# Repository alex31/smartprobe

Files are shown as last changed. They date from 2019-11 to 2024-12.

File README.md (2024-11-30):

# SMARTPROBE Pitot3D device

Smartprobe is an autonomous pitot3d tube that is designed to be mounted on a drone.
It records relative wind speed and angles, stores them on sdcard, and stream data on a serial line.

#### *Disclaimer : software was still in alpha stage when the project development was stopped in fall 2021*

## Installation

### The easy way
use the latest binary found under GitHub Releases

### You really want to compile it ?
### Dependencies installation 

>cross compilation and Perl library for the boardGen.pl tool :

``` shell
sudo apt install build-essential gcc-arm-none-eabi gdb-multiarch \
         default-jre libmodern-perl-Perl \
	 libxml-libxml-Perl libfile-which-Perl \
	 dfu-util
	 
sudo cpan -i String/LCSS.pm
```
> to use bmpflash when flashing with a Black Magic Probe or Criquet Probe
``` shell
sudo usermod -a -G dialout $USER
```
### optional : stm32cubemx install from stmicroelectronics website:
https://www.st.com/en/development-tools/stm32cubemx.html
(boardGen.pl script needs xml MCU description files)
If stm32cubemx is not found, a pregenerated board.h is used, you won't be able to modify pin assignation

### clone of GitHub repository and submodules :
``` shell
git clone --recursive https://github.com/alex31/smartprobe.git
cd smartprobe
git submodule update --init --recursive
```

### build firmware in release mode
``` shell
make clean; make BUILD=SIZE
```

### flash firmware in release mode
In dfu mode :
plug micro-USB cable (no need to power supply)
``` shell
make BUILD=SIZE dfuflash

```
In swd mode :
plug swd cable (need to power supply smartprobe)
``` shell
make BUILD=SIZE flash
``` 

## Usage

### µSD Card
It is mandatory to install a micro sd card :
- SD should be formatted with FAT32 or ExFAT filesystem.
- configuration is read from SD
- wind data is stored on the SD
- reading/writing SD can be done
  - offline : SD must be removed
  - online : plug the smartprobe via USB (with SD installed) on a computer, and it will be shown like a USB storage device

### Connector J3 at the back
The Molex connector at the back contains  :  
- power in : Vin should be between 7 and 20 Volts
- bootloader mode switch (connect pin5 with pin6, then power up the smartprobe)
  -bootloader mode is to be used to flash the firmware in the smartprobe
- USB to mount the sdcard as a USB storage device
- UART which can be used for multiple purposes (choice is made in configuration file)

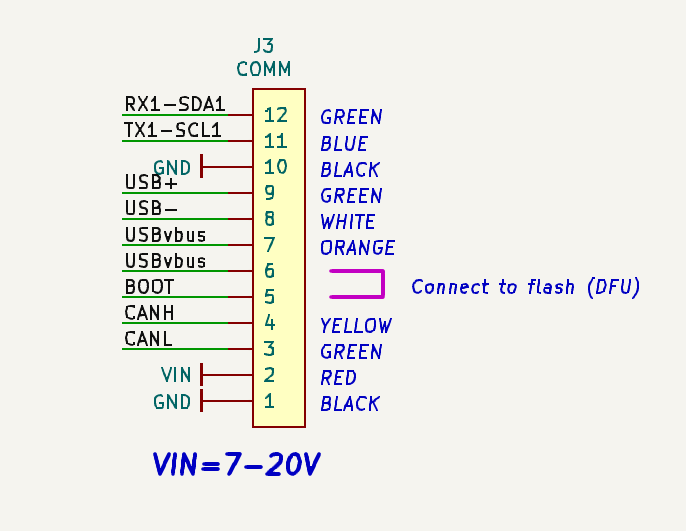
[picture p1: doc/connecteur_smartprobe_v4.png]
Molex connector wiring
  

### Parameters
- firmware parameters are read from the SD at start, in a file named ***smartprobe.conf***
- if a file named smartprobe.conf is not found, it will be created, all the fields set at their default value
- the most accurate and up-to-date definitions (with default and range) for each field can be found in source file  
*source/confParameters.hpp*
- here is a list of parameters (details are missing, confParameters.hpp reading is advised)

|Parameter				| Description 	| default 
|---				| ---  	| ---
|syslog.filename			| name of the file where system events are logged	|syslog
|sensorslog.filename			| name of the file where sensors data are logged	|sensors
|thread.frequency.d_press		| differential pressure sampling frequency  		|100
|thread.frequency.imu			| IMU sampling frequency 				|100
|thread.frequency.stream_console	| frequency of messages on the console			|10
|thread.frequency.transmit_uart		| frequency of messages on serial link			|100
|ahrs.type				| type of AHRS : raw, headless, or complete		|headless_ahrs
|ahrs.output				| ahrs output format : euler or quaternion		|euler
|uart.mode				| no_used or pprz or nmea_in or ubx_in			|pprz
|pprz.message				| pprz msg to stream data : aeroprobe or smartprobe	|aeroprobe
|uart.baud				| Baud rate of the uart in the range 9600..460800	|115200
|canbus.mode				| not yet implemented					|
|canbus.id				| not yet implemented					|
|sensor.barometer.temperatureBias	| temperature bias of the measured exterior air		|-5
|sensor.barometer.lpf			| barometer clock divider (see LPS33HW datasheet)	|div2
|sensor.barometer.odr			| barometer output data rate (see LPS33HW datasheet)	|50hz
|sensor.d_press.fetched			| diff pressure param fetched : press or press + temp	|P+T
|sensor.d_press.fetchTempFrequency	| diff pressure temp frequency fetching			|1<<
|sensor.imu.accrate			| imu acc fetching rate (see ICM20600 datasheet)	|1khz_bw99
|sensor.imu.gyrorange			| gyro range [250 .. 2000] degrees per seconds		|250_dps
|sensor.imu.accrange			| acc range [2 .. 16] G					|2g
|sensor.imu.estimationLoopDuration_ms	| ahrs calibration duration [10 .. 4000] milliseconds	|500
|airspeed.rho				| estimated (0) or fixed in the range [0.1 .. 2]	|0(force estimation)
|airspeed.calibration.m11		| transformation matrix	from the			|1.15
|airspeed.calibration.m12		| calibration process					|0
|airspeed.calibration.m13		| default values can be used to verify that		|0
|airspeed.calibration.m14		| the smartprobe roughly works, but should not be	|6
|airspeed.calibration.m15		| used to make actual measures				|6
|airspeed.calibration.m21		| 							|0
|airspeed.calibration.m22		| 							|15
|airspeed.calibration.m23		| 							|0
|airspeed.calibration.m24		| 							|0
|airspeed.calibration.m25		| 							|0
|airspeed.calibration.m31		| 							|0
|airspeed.calibration.m32		| 							|0
|airspeed.calibration.m33		| 							|11
|airspeed.calibration.m34		| 							|0
|airspeed.calibration.m35		|		 					|0
|airspeed.calibration.bias.velocity	|bias on air velocity (from calibration)		|0
|airspeed.calibration.bias.alpha	|bias on alfa angle (from calibration)			|0
|airspeed.calibration.bias.beta 	|bias on beta angle (from calibration)			|0
|led.mode				|status or airspeed					|status
|					|							|

## Calibration
Smartprobe should be calibrated in a wind tunnel before use. The calibration matrix values should then be written in the configuration file instead of the default values.

### Calibration procedure :
...TO BE WRITTEN...

## Development tool
there is a SWD connector on the PCB for connecting a debug probe (Black Magic Probe or STlink V2/V3) which permits debugging with gdb and access to a shell console where errors messages are shown.

## troubleshooting
The led color reflect status of operation (see details below). When error occurs, the error details are logged in the syslog file, on the sdcard, and on debug console if a probe is attached to the internal swd+serial connector.

#### error codes :
- blink green : OK
- blink green and orange : sd card file system is dirty, operation will try to continue, but ultimately, there is a need for filesystem check or reformating
- blink orange : sd card mount has failed
- blink green and white : configuration file error
- blink red : hardware fault detected

..
## Ideas for future developments 
- If external componant (autopilot) stream gps positions and heading, wind in a terrestrial reference frame could be calculated on board
- add USB CDC endoint to the existing USB storage endpoint to output serial console shell via USB
- stream UAVCAN messages on the CAN 2.0B interface

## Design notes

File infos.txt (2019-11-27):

             _______           _____                   
            |__   __|         |  __ \                  
               | |      ___   | |  | |    ___          
               | |     / _ \  | |  | |   / _ \         
               | |    | (_) | | |__| |  | (_) |        
               |_|     \___/  |_____/    \___/         

   ° fix
        * tester fix frozen
	* workerClass.hpp :
	  ø faire l'init en thread context (necessaire pour les event listener, mutex, ...)
	  ø run : remplacer while (true) {...}  par do {...} while (time != TIME_INFINITE)
	* remplacer les DebugTrace par des logError(severity, "string")
	* log de la revision de firmware sha git + date/time de compilation
	* remplacer le log de compteur par des données capteur
	* recoder la partie  FCNTL_WRITE de sdLog.c pour factoriser le code

   ° écrire des modules

	* lecture fichier de conf
	* version qui envoie les données brutes sur la liaison série et la sdcard pour Murat
	* ahrs 2 angles (sans compas)
	* eigen ?
	* watchdog IWDG -> test au boot, si il y a eu hardfault -> log
	* recup de données gps -> ref horaire, calcul du cap, choix du format dans le fichier de conf :
	  ø nmea ou trame pprz (ou autre ?)
	* embarquer micro python pour coder du comportement via le fichier de conf sans avoir à reflasher ?

             _____     __  __    ___          
            |  __ \   |  \/  |  / _ \         
            | |  | |  | \  / | | |_| |        
            | |  | |  | |\/| | |  _  |        
            | |__| |  | |  | | | | | |        
            |_____/   |_|  |_| |_| |_|        
                    _                                                     
                   | |                                                    
             ___   | |_    _ __    ___    __ _   _ __ ___    ___          
            / __|  | __|  | '__|  / _ \  / _` | | '_ ` _ \  / __|         
            \__ \  \ |_   | |    |  __/ | (_| | | | | | | | \__ \         
            |___/   \__|  |_|     \___|  \__,_| |_| |_| |_| |___/         

#define STM32_ADC_ADC1_DMA_STREAM           STM32_DMA_STREAM_ID(2, 4)
#define STM32_SDC_SDMMC1_DMA_STREAM         STM32_DMA_STREAM_ID(2, 6)
#define STM32_SPI_SPI1_RX_DMA_STREAM        STM32_DMA_STREAM_ID(2, 0)
#define STM32_SPI_SPI1_TX_DMA_STREAM        STM32_DMA_STREAM_ID(2, 3)
#define STM32_I2C_I2C2_RX_DMA_STREAM        STM32_DMA_STREAM_ID(1, 3)
#define STM32_I2C_I2C2_TX_DMA_STREAM        STM32_DMA_STREAM_ID(1, 7)
#define STM32_I2C_I2C4_RX_DMA_STREAM        STM32_DMA_STREAM_ID(1, 2)
#define STM32_I2C_I2C4_TX_DMA_STREAM        STM32_DMA_STREAM_ID(1, 5)

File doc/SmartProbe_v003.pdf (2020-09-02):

## SmartProbe_v003 Project Configuration Report

# 1. Description

## 1.1. Project

Project Name | SmartProbe_v003
Board Name | custom
Generated with: | STM32CubeMX 5.6.0
Date | 03/17/2020

## 1.2. MCU

MCU Series | STM32F7
MCU Line | STM32F7x7
MCU name | STM32F777VIHx
MCU Package | TFBGA100
MCU Pin number | 100

# 2. Pinout Configuration

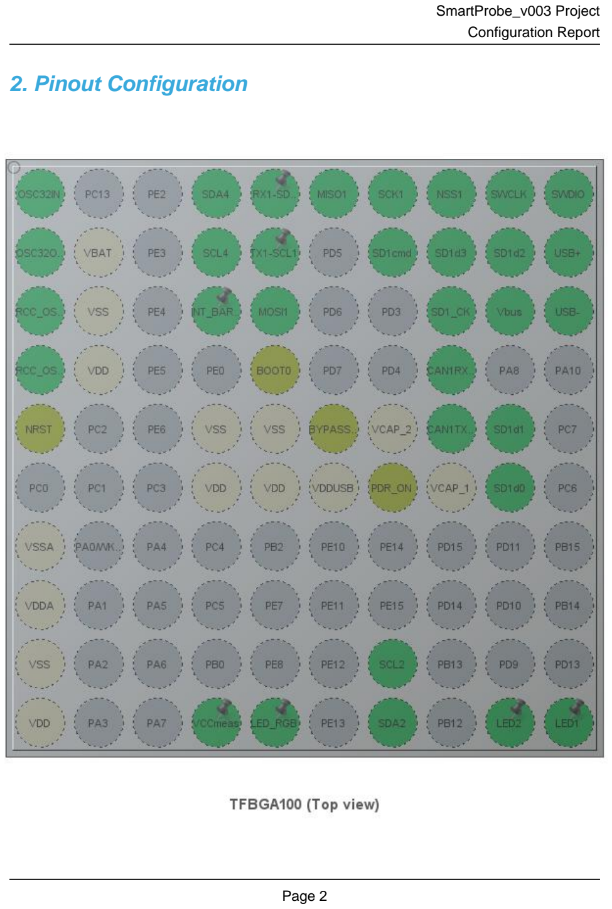
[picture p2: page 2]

# 3. Pins Configuration

Pin Number TFBGA100 | Pin Name (function after reset) | Pin Type | Alternate Function(s) | Label
A1 | PC14/OSC32_IN | I/O | RCC_OSC32_IN | OSC32IN
A4 | PB9 | I/O | I2C4_SDA | SDA4
A5 | PB7 | I/O | USART1_RX | RX1-SDA1
A6 | PB4 | I/O | SPI1_MISO | MISO1
A7 | PB3 | I/O | SPI1_SCK | SCK1
A8 | PA15 | I/O | SPI1_NSS | NSS1
A9 | PA14 | I/O | SYS_JTCK-SWCLK | SWCLK
A10 | PA13 | I/O | SYS_JTMS-SWDIO | SWDIO
B1 | PC15/OSC32_OUT | I/O | RCC_OSC32_OUT | OSC32OUT
B2 | VBAT | Power
B4 | PB8 | I/O | I2C4_SCL | SCL4
B5 | PB6 | I/O | USART1_TX | TX1-SCL1
B7 | PD2 | I/O | SDMMC1_CMD | SD1cmd
B8 | PC11 | I/O | SDMMC1_D3 | SD1d3
B9 | PC10 | I/O | SDMMC1_D2 | SD1d2
B10 | PA12 | I/O | USB_OTG_FS_DP | USB+
C1 | PH0/OSC_IN | I/O | RCC_OSC_IN
C2 | VSS | Power
C4 | PE1 * | I/O | GPIO_Input | INT_BARO
C5 | PB5 | I/O | SPI1_MOSI | MOSI1
C8 | PC12 | I/O | SDMMC1_CK | SD1_CK
C9 | PA9 | I/O | USB_OTG_FS_VBUS | Vbus
C10 | PA11 | I/O | USB_OTG_FS_DM | USB-
D1 | PH1/OSC_OUT | I/O | RCC_OSC_OUT
D2 | VDD | Power
D5 | BOOT0 | Boot
D8 | PD0 | I/O | CAN1_RX | CAN1RX-RX4
E1 | NRST | Reset
E4 | VSS | Power
E5 | VSS | Power
E6 | BYPASS_REG | Reset
E7 | VCAP_2 | Power
E8 | PD1 | I/O | CAN1_TX | CAN1TX-TX4
E9 | PC9 | I/O | SDMMC1_D1 | SD1d1
F4 | VDD | Power
F5 | VDD | Power

Pin Number TFBGA100 | Pin Name (function after reset) | Pin Type | Alternate Function(s) | Label
F6 | VDDUSB | Power
F7 | PDR_ON | Reset
F8 | VCAP_1 | Power
F9 | PC8 | I/O | SDMMC1_D0 | SD1d0
G1 | VSSA | Power
H1 | VDDA | Power
J1 | VSS | Power
J7 | PB10 | I/O | I2C2_SCL | SCL2
K1 | VDD | Power
K4 | PB1 | I/O | ADC1_IN9 | VCCmeas
K5 | PE9 | I/O | TIM1_CH1 | LED_RGB
K7 | PB11 | I/O | I2C2_SDA | SDA2
K9 | PD8 * | I/O | GPIO_Output | LED2
K10 | PD12 * | I/O | GPIO_Output | LED1

## * The pin is affected with an I/O function

# 4. Clock Tree Configuration

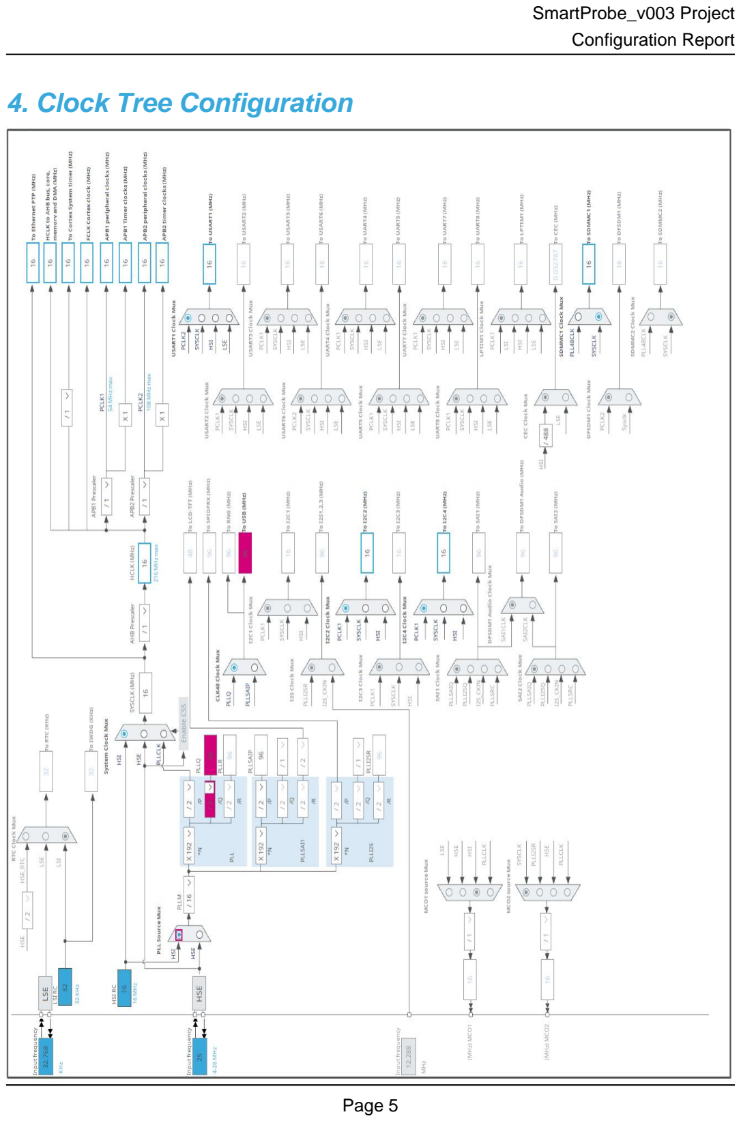
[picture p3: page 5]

# 5. Software Project

## 5.1. Project Settings

Name | Value
Project Name | SmartProbe_v003
Project Folder | /home/alex/DEV/STM32/CHIBIOS/C19DEV/SMARTPROBE_M777/smart_probe
Toolchain / IDE | EWARM V8.32
Firmware Package Name and Version | STM32Cube FW_F7 V1.15.0

## 5.2. Code Generation Settings

Name | Value
STM32Cube MCU packages and embedded software | Copy all used libraries into the project folder
Generate peripheral initialization as a pair of '.c/.h' files | No
Backup previously generated files when re-generating | No
Delete previously generated files when not re-generated | Yes
Set all free pins as analog (to optimize the power consumption) | No

# 6. Power Consumption Calculator report

### 6.1. Microcontroller Selection

Series | STM32F7
Line | STM32F7x7
MCU | STM32F777VIHx
Datasheet | 028294_Rev4

### 6.2. Parameter Selection

Temperature | 25
Vdd | 3.3

### 6.3. Battery Selection

Battery | Alkaline(9V)
Capacity | 625.0 mAh
Self Discharge | 0.3 %/month
Nominal Voltage | 9.0 V
Max Cont Current | 200.0 mA
Max Pulse Current | 0.0 mA
Cells in series | 1
Cells in parallel | 1

## 6.4. Sequence

Step | Step1 | Step2
Mode | RUN | STOP_UDM (Under Drive)
Vdd | 3.3 | 3.3
Voltage Source | Battery | Battery
Range | Scale1-High | No Scale
Fetch Type | ICTM FLASH-SingleBank REGON | n/a
CPU Frequency | 216 MHz | 0 Hz
Clock Configuration | HSE PLL | Regulator_LP Flash-PwrDwn
Clock Source Frequency | 4 MHz | 0 Hz

### Peripherals

Additional Cons. | 0 mA | 0 mA
Average Current | 118 mA | 130 µA
Duration | 0.1 ms | 0.9 ms
DMIPS | 462.0 | 0.0
Ta Max | 88.26 | 104.98
Category | In DS Table | In DS Table

## 6.5. RESULTS

Sequence Time | 1 ms | Average Current | 11.92 mA
Battery Life | 2 days, 4 hours | Average DMIPS | 462.24 DMIPS

## 6.6. Chart

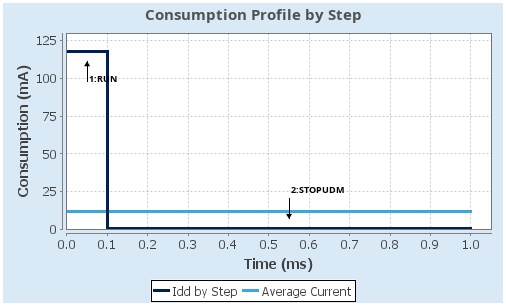
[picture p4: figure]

# 7. IPs and Middleware Configuration

# 7.1. ADC1

## mode: IN9 7.1.1. Parameter Settings:

### ADCs_Common_Settings:

Mode | Independent mode

### ADC_Settings:

Clock Prescaler | PCLK2 divided by 2
Resolution | 12 bits (15 ADC Clock cycles)
Data Alignment | Right alignment
Scan Conversion Mode | Disabled
Continuous Conversion Mode | Disabled
Discontinuous Conversion Mode | Disabled
DMA Continuous Requests | Disabled
End Of Conversion Selection | EOC flag at the end of single channel conversion

### ADC_Regular_ConversionMode:

Number Of Conversion | 1
External Trigger Conversion Source | Regular Conversion launched by software
External Trigger Conversion Edge | None
Rank | 1
Channel | Channel 9
Sampling Time | 3 Cycles

### ADC_Injected_ConversionMode:

Number Of Conversions | 0

### WatchDog:

Enable Analog WatchDog Mode | false

# 7.2. CAN1

## mode: Mode 7.2.1. Parameter Settings:

### Bit Timings Parameters:

Prescaler (for Time Quantum) | 16
Time Quantum | 1000.0 *
Time Quanta in Bit Segment 1 | 1 Time
Time Quanta in Bit Segment 2 | 1 Time

ReSynchronization Jump Width | 1 Time

### Basic Parameters:

Time Triggered Communication Mode | Disable
Automatic Bus-Off Management | Disable
Automatic Wake-Up Mode | Disable
Automatic Retransmission | Disable
Receive Fifo Locked Mode | Disable
Transmit Fifo Priority | Disable

### Advanced Parameters:

Operating Mode | Normal

# 7.3. GPIO

# 7.4. I2C2

## I2C: I2C 7.4.1. Parameter Settings:

### Timing configuration:

I2C Speed Mode | Standard Mode
I2C Speed Frequency (KHz) | 100
Rise Time (ns) | 0
Fall Time (ns) | 0
Coefficient of Digital Filter | 0
Analog Filter | Enabled
Timing | 0x00303D5B

### Slave Features:

Clock No Stretch Mode | Disabled
General Call Address Detection | Disabled
Primary Address Length selection | 7-bit
Dual Address Acknowledged | Disabled
Primary slave address | 0

# 7.5. I2C4

## I2C: I2C 7.5.1. Parameter Settings:

### Timing configuration:

I2C Speed Mode | Standard Mode
I2C Speed Frequency (KHz) | 100
Rise Time (ns) | 0
Fall Time (ns) | 0
Coefficient of Digital Filter | 0
Analog Filter | Enabled
Timing | 0x00303D5B

### Slave Features:

Clock No Stretch Mode | Disabled
General Call Address Detection | Disabled
Primary Address Length selection | 7-bit
Dual Address Acknowledged | Disabled
Primary slave address | 0

# 7.6. RCC

## High Speed Clock (HSE): Crystal/Ceramic Resonator Low Speed Clock (LSE) : Crystal/Ceramic Resonator 7.6.1. Parameter Settings:

### System Parameters:

VDD voltage (V) | 3.3
Flash Latency(WS) | 0 WS (1 CPU cycle)

### RCC Parameters:

HSI Calibration Value | 16
TIM Prescaler Selection | Disabled
HSE Startup Timout Value (ms) | 100
LSE Startup Timout Value (ms) | 5000

### Power Parameters:

Power Over Drive | Disabled
Power Regulator Voltage Scale | Power Regulator Voltage Scale 3

# 7.7. SDMMC1

## Mode: SD 4 bits Wide bus 7.7.1. Parameter Settings:

### SDMMC parameters:

Clock transition on which the bit capture is made Rising transition

SDMMC Clock divider bypass | Disable
SDMMC Clock output enable when the bus is idle | Disable the power save for the clock
SDMMC hardware flow control | The hardware control flow is disabled
SDMMCCLK clock divide factor | 0

# 7.8. SPI1

## Mode: Full-Duplex Master Hardware NSS Signal: Hardware NSS Output Signal 7.8.1. Parameter Settings:

### Basic Parameters:

Frame Format | Motorola
Data Size | 4 Bits
First Bit | MSB First

### Clock Parameters:

Prescaler (for Baud Rate) | 2
Baud Rate | 8.0 MBits/s *
Clock Polarity (CPOL) | Low
Clock Phase (CPHA) | 1 Edge

### Advanced Parameters:

CRC Calculation | Disabled
NSSP Mode | Enabled
NSS Signal Type | Output Hardware

# 7.9. SYS

## Debug: Serial Wire Timebase Source: SysTick

# 7.10. TIM1

## Channel1: PWM Generation CH1 7.10.1. Parameter Settings:

### Counter Settings:

Prescaler (PSC - 16 bits value) | 0
Counter Mode | Up
Counter Period (AutoReload Register - 16 bits value ) | 0

Internal Clock Division (CKD) | No Division
Repetition Counter (RCR - 16 bits value) | 0
auto-reload preload | Disable

### Trigger Output (TRGO) Parameters:

Master/Slave Mode (MSM bit) | Disable (Trigger input effect not delayed)
Trigger Event Selection TRGO | Reset (UG bit from TIMx_EGR)
Trigger Event Selection TRGO2 | Reset (UG bit from TIMx_EGR)

### Break And Dead Time management - BRK Configuration:

BRK State | Disable
BRK Polarity | High
BRK Filter (4 bits value) | 0
BRK Sources Configuration
- Digital Input | Disable
- DFSDM | Disable

### Break And Dead Time management - BRK2 Configuration:

BRK2 State | Disable
BRK2 Polarity | High
BRK2 Filter (4 bits value) | 0
BRK2 Sources Configuration
- Digital Input | Disable
- DFSDM | Disable

### Break And Dead Time management - Output Configuration:

Automatic Output State | Disable
Off State Selection for Run Mode (OSSR) | Disable
Off State Selection for Idle Mode (OSSI) | Disable
Lock Configuration | Off

### PWM Generation Channel 1:

Mode | PWM mode 1
Pulse (16 bits value) | 0
Output compare preload | Enable
Fast Mode | Disable
CH Polarity | High
CH Idle State | Reset

# 7.11. USART1

## Mode: Asynchronous 7.11.1. Parameter Settings:

### Basic Parameters:

Baud Rate | 115200
Word Length | 8 Bits (including Parity)
Parity | None
Stop Bits | 1

### Advanced Parameters:

Data Direction | Receive and Transmit
Over Sampling | 16 Samples
Single Sample | Disable

### Advanced Features:

Auto Baudrate | Disable
TX Pin Active Level Inversion | Disable
RX Pin Active Level Inversion | Disable
Data Inversion | Disable
TX and RX Pins Swapping | Disable
Overrun | Enable
DMA on RX Error | Enable
MSB First | Disable

# 7.12. USB_OTG_FS

## Mode: Device_Only mode: Activate_VBUS 7.12.1. Parameter Settings:

Speed | Device Full Speed 12MBit/s
Low power | Disabled
Link Power Management | Disabled
VBUS sensing | Enabled
Signal start of frame | Disabled

### * User modified value

# 8. System Configuration

# 8.1. GPIO configuration

IP | Pin | Signal | GPIO mode | GPIO pull/up pull down | Max Speed | User Label
ADC1 | PB1 | ADC1_IN9 | Analog mode | No pull-up and no pull-down | n/a | VCCmeas
CAN1 | PD0 | CAN1_RX | Alternate Function Push Pull | No pull-up and no pull-down | Very High * | CAN1RX-RX4
| PD1 | CAN1_TX | Alternate Function Push Pull | No pull-up and no pull-down | Very High * | CAN1TX-TX4
I2C2 | PB10 | I2C2_SCL | Alternate Function Open Drain | Pull-up | Very High * | SCL2
| PB11 | I2C2_SDA | Alternate Function Open Drain | Pull-up | Very High * | SDA2
I2C4 | PB9 | I2C4_SDA | Alternate Function Open Drain | Pull-up | Very High * | SDA4
| PB8 | I2C4_SCL | Alternate Function Open Drain | Pull-up | Very High * | SCL4
RCC | PC14/OSC3 2_IN | RCC_OSC32_IN | n/a | n/a | n/a | OSC32IN
| PC15/OSC3 2_OUT | RCC_OSC32_O UT | n/a | n/a | n/a | OSC32OUT
| PH0/OSC_I N | RCC_OSC_IN | n/a | n/a | n/a
| PH1/OSC_O UT | RCC_OSC_OUT | n/a | n/a | n/a
SDMMC1 | PD2 | SDMMC1_CMD | Alternate Function Push Pull | No pull-up and no pull-down | Very High | SD1cmd
| PC11 | SDMMC1_D3 | Alternate Function Push Pull | No pull-up and no pull-down | Very High | SD1d3
| PC10 | SDMMC1_D2 | Alternate Function Push Pull | No pull-up and no pull-down | Very High | SD1d2
| PC12 | SDMMC1_CK | Alternate Function Push Pull | No pull-up and no pull-down | Very High | SD1_CK
| PC9 | SDMMC1_D1 | Alternate Function Push Pull | No pull-up and no pull-down | Very High | SD1d1
| PC8 | SDMMC1_D0 | Alternate Function Push Pull | No pull-up and no pull-down | Very High | SD1d0
SPI1 | PB4 | SPI1_MISO | Alternate Function Push Pull | No pull-up and no pull-down | Very High * | MISO1
| PB3 | SPI1_SCK | Alternate Function Push Pull | No pull-up and no pull-down | Very High * | SCK1
| PA15 | SPI1_NSS | Alternate Function Push Pull | No pull-up and no pull-down | Very High * | NSS1
| PB5 | SPI1_MOSI | Alternate Function Push Pull | No pull-up and no pull-down | Very High * | MOSI1

IP | Pin | Signal | GPIO mode | GPIO pull/up pull down | Max Speed | User Label
SYS | PA14 | SYS_JTCK-SWCLK | n/a | n/a | n/a | SWCLK
| PA13 | SYS_JTMS-SWDIO | n/a | n/a | n/a | SWDIO
TIM1 | PE9 | TIM1_CH1 | Alternate Function Push Pull | No pull-up and no pull-down | Low | LED_RGB
USART1 | PB7 | USART1_RX | Alternate Function Push Pull | No pull-up and no pull-down | Very High * | RX1-SDA1
| PB6 | USART1_TX | Alternate Function Push Pull | No pull-up and no pull-down | Very High * | TX1-SCL1
USB_OTG_ FS | PA12 | USB_OTG_FS_ DP | Alternate Function Push Pull | No pull-up and no pull-down | Very High * | USB+
| PA9 | USB_OTG_FS_ VBUS | Input mode | No pull-up and no pull-down | n/a | Vbus
| PA11 | USB_OTG_FS_ DM | Alternate Function Push Pull | No pull-up and no pull-down | Very High * | USB-
GPIO | PE1 | GPIO_Input | Input mode | No pull-up and no pull-down | n/a | INT_BARO
| PD8 | GPIO_Output | Output Push Pull | No pull-up and no pull-down | Low | LED2
| PD12 | GPIO_Output | Output Push Pull | No pull-up and no pull-down | Low | LED1

# 8.2. DMA configuration

DMA request | Stream | Direction | Priority
TIM1_CH1 | DMA2_Stream1 | Memory To Peripheral | Low

## TIM1_CH1: DMA2_Stream1 DMA request Settings:

Mode: | Normal
Use fifo: | Disable
Peripheral Increment: | Disable
Memory Increment: | Enable *
Peripheral Data Width: | Half Word
Memory Data Width: | Half Word

# 8.3. NVIC configuration

Interrupt Table | Enable | Preenmption Priority | SubPriority
Non maskable interrupt | true | 0 | 0
Hard fault interrupt | true | 0 | 0
Memory management fault | true | 0 | 0
Pre-fetch fault, memory access fault | true | 0 | 0
Undefined instruction or illegal state | true | 0 | 0
System service call via SWI instruction | true | 0 | 0
Debug monitor | true | 0 | 0
Pendable request for system service | true | 0 | 0
System tick timer | true | 0 | 0
DMA2 stream1 global interrupt | true | 0 | 0
PVD interrupt through EXTI line 16 | unused
Flash global interrupt | unused
RCC global interrupt | unused
ADC1, ADC2 and ADC3 global interrupts | unused
CAN1 TX interrupts | unused
CAN1 RX0 interrupts | unused
CAN1 RX1 interrupt | unused
CAN1 SCE interrupt | unused
TIM1 break interrupt and TIM9 global interrupt | unused
TIM1 update interrupt and TIM10 global interrupt | unused
TIM1 trigger and commutation interrupts and TIM11 global interrupt | unused
TIM1 capture compare interrupt | unused
I2C2 event interrupt | unused
I2C2 error interrupt | unused
SPI1 global interrupt | unused
USART1 global interrupt | unused
SDMMC1 global interrupt | unused
USB On The Go FS global interrupt | unused
FPU global interrupt | unused
I2C4 event interrupt | unused
I2C4 error interrupt | unused

### * User modified value

# 9. Predefined Views - Category view : Current

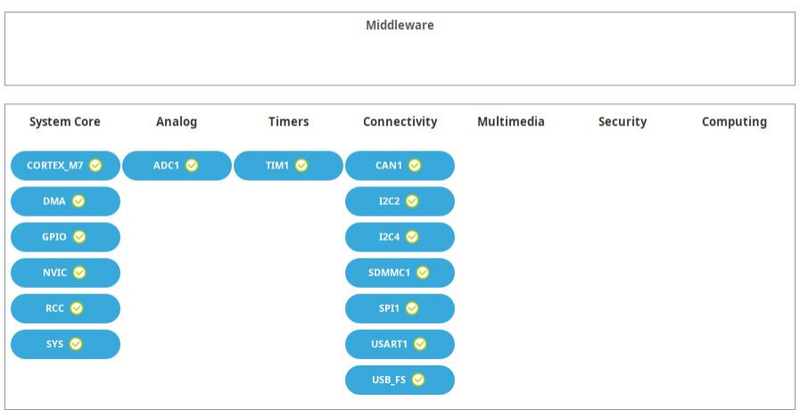
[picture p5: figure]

# 10. Software Pack Report

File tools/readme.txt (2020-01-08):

utilisation de l'interface graphique associée à la smartprobe :

* flasher une smartprobe avec la dernière version du firmware de la branche
  with_ahrs_and_eigen"

* brancher une blackmagic probe pour avoir un convertisseur usb serie

* par defaut, les messages de sortie sont émis, donc rien à faire de ce côté là.

* lancer le script spGui.pl

* ordre des bargraphs : pression absolue, diff1, diff2, diff3

* tout à droite il y a un scale qui permet de regler le gain au niveau de
  l'affichage de la pression differentielle.

* en // les données sont logguées sur la carte SD en fonction des paramètres lu sur le
  fichier smartprobe.conf à la racine de la carte SD

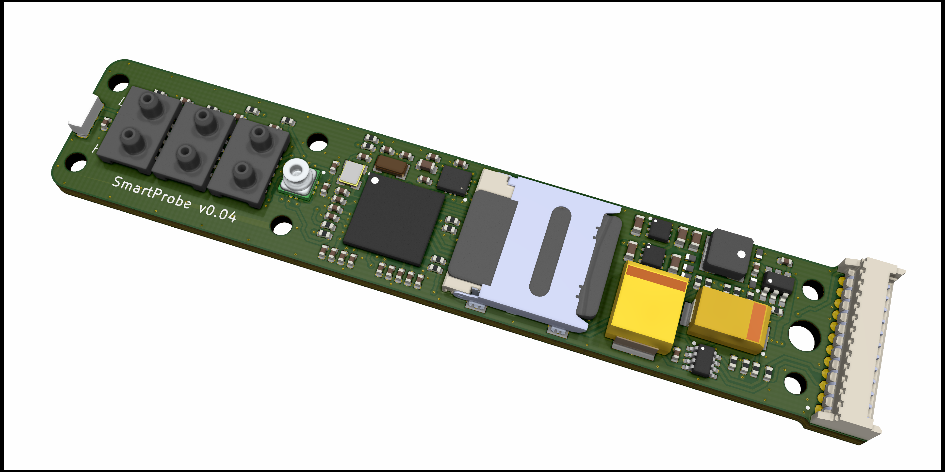
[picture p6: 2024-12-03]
hardware/Pictures/SmartProbe_v004_pcb_top_view.png

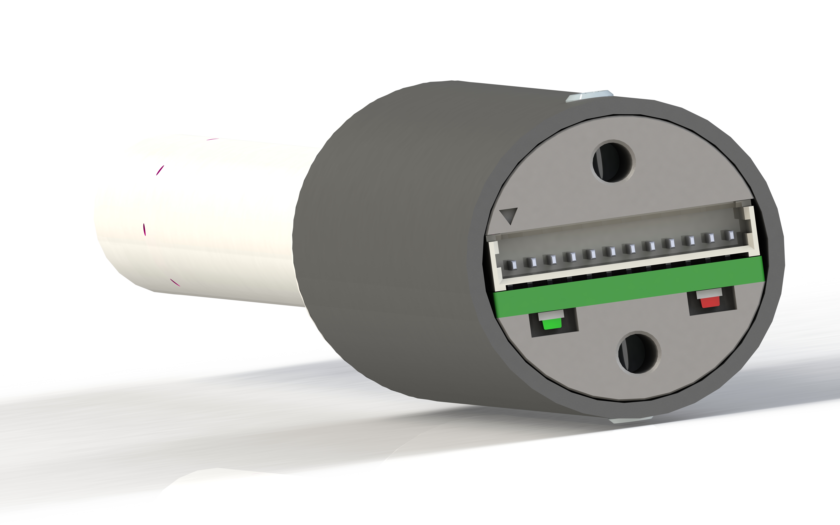
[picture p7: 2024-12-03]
hardware/Pictures/SmartProbe_v004_view7.JPG

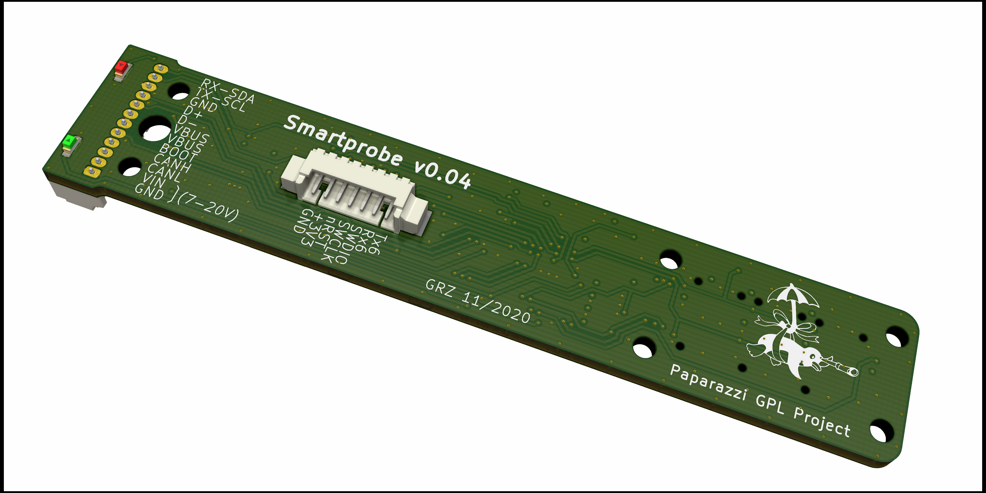
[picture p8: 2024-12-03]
hardware/Pictures/SmartProbe_v004_pcb_bottom_view.png

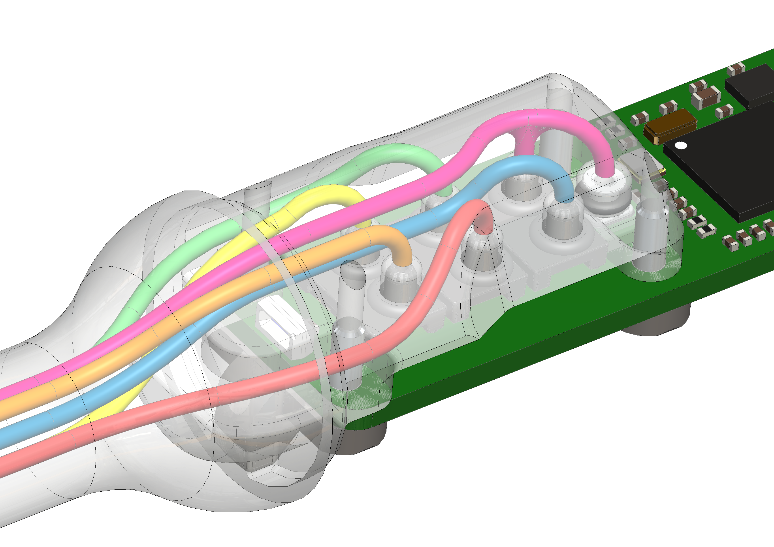
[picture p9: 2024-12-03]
hardware/Pictures/SmartProbe_v004_view4.PNG

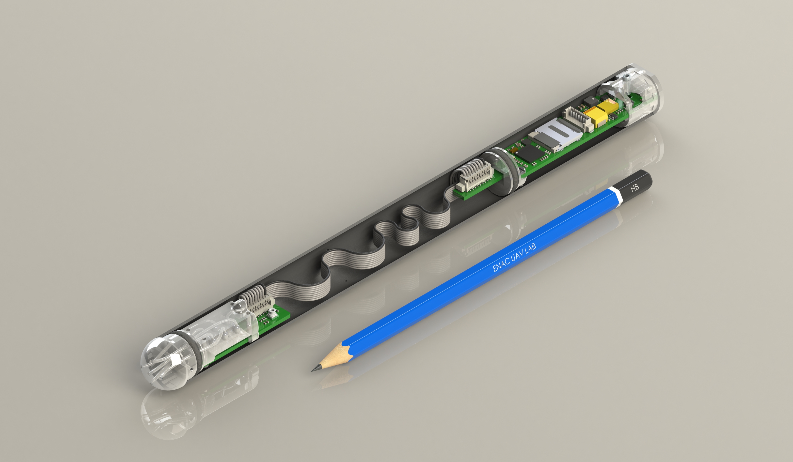
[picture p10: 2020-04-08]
doc/SmartProbe_v003_pencil_1.JPG

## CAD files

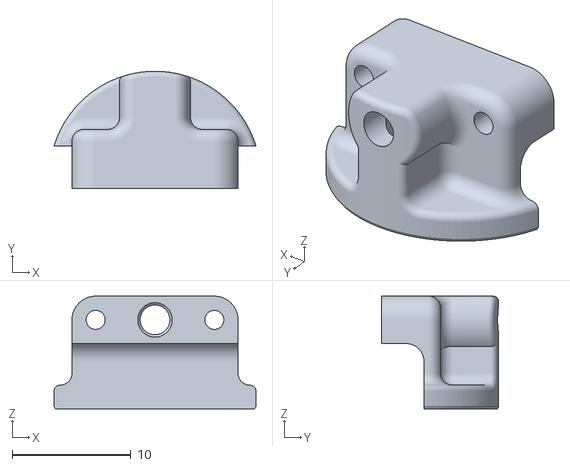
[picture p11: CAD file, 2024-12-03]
hardware/Mechanics/SmartProbe_v004_cap.STL
17.0 x 9.90 x 9.50

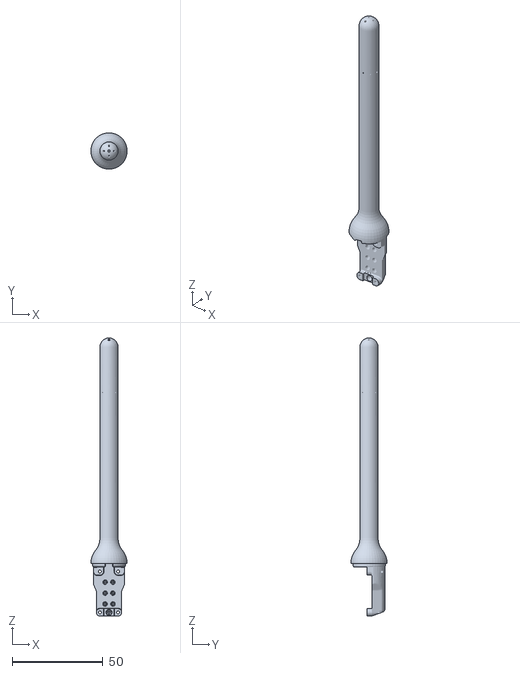
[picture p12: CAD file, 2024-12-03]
hardware/Mechanics/SmartProbe_v004_noze.STL
20.0 x 19.9 x 153.0

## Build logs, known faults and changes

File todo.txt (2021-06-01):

             _______           _____                   
            |__   __|         |  __ \                  
               | |      ___   | |  | |    ___          
               | |     / _ \  | |  | |   / _ \         
               | |    | (_) | | |__| |  | (_) |        
               |_|     \___/  |_____/    \___/         

A CODER:

        * en fonction du choix du format de sortie de l'ahrs :
	  + sortir dans le bon format pour sd (mais pas terminal qui reste en euler)
	  + sortir en pascal au lieu de hPa partout (sd et serial) mais pas terminal qui reste en hPa
	  + sortir en radian partout mais pas terminal qui reste en degrés

	* implementer une directive include dans confFile
	  * mettre les données de calibration dans cet include en rajoutant
	    un parametre "nom de calibration"

	* utilisation du buscan pour chainer les smartprobes

	* ahrs complet qui donne 3 angles si la donnée cap est disponible 

	* calcul d'un vecteur vent dans le repaire terrestre si l'ahrs est
	  en mode 3 angles et que
	   1/ l'autopilote fournit un vecteur vitesse en 3D
	   ou
	   2/ un gps est connecté et permet de calculer le vecteur vitesse en 3D

A AMELIORER :

	* rationaliser utilisation d'allocateur dynamique  :
	  celui de newlib ou tlsf, eliminuer celui de chibios
	* (LOW PRIO) utiliser module UART (DMA) au lieu de serial pour
	             les I/O sur la liaison série ?

	* amélioration des perfos :
    	  + utiliser c++ fmt au lieu de cstdio dans le cas du log texte

        * watchdog IWDG -> test au boot, si il y a eu hardfault -> log

GRANDES LIGNES : 

   ° integration de librairies externes
	* coder du comportement via le fichier de conf sans avoir à reflasher :
	  +  micro python ?
	     OU
	  + langage adhoc en utilisant un parser et un lexer ?

             _____     __  __    ___          
            |  __ \   |  \/  |  / _ \         
            | |  | |  | \  / | | |_| |        
            | |  | |  | |\/| | |  _  |        
            | |__| |  | |  | | | | | |        
            |_____/   |_|  |_| |_| |_|        
                    _                                                     
                   | |                                                    
             ___   | |_    _ __    ___    __ _   _ __ ___    ___          
            / __|  | __|  | '__|  / _ \  / _` | | '_ ` _ \  / __|         
            \__ \  \ |_   | |    |  __/ | (_| | | | | | | | \__ \         
            |___/   \__|  |_|     \___|  \__,_| |_| |_| |_| |___/         

#define STM32_ADC_ADC1_DMA_STREAM           STM32_DMA_STREAM_ID(2, 4)
#define STM32_TIM1_UP_DMA_STREAM	    STM32_DMA_STREAM_ID(2, 5)
#define STM32_TIM1_UP_DMA_CHANNEL	    6
#define STM32_SDC_SDMMC1_DMA_STREAM         STM32_DMA_STREAM_ID(2, 6)
#define STM32_SPI_SPI1_RX_DMA_STREAM        STM32_DMA_STREAM_ID(2, 0)
#define STM32_SPI_SPI1_TX_DMA_STREAM        STM32_DMA_STREAM_ID(2, 3)
#define STM32_I2C_I2C2_RX_DMA_STREAM        STM32_DMA_STREAM_ID(1, 3)
#define STM32_I2C_I2C2_TX_DMA_STREAM        STM32_DMA_STREAM_ID(1, 7)
#define STM32_I2C_I2C4_RX_DMA_STREAM        STM32_DMA_STREAM_ID(1, 2)
#define STM32_I2C_I2C4_TX_DMA_STREAM        STM32_DMA_STREAM_ID(1, 5)

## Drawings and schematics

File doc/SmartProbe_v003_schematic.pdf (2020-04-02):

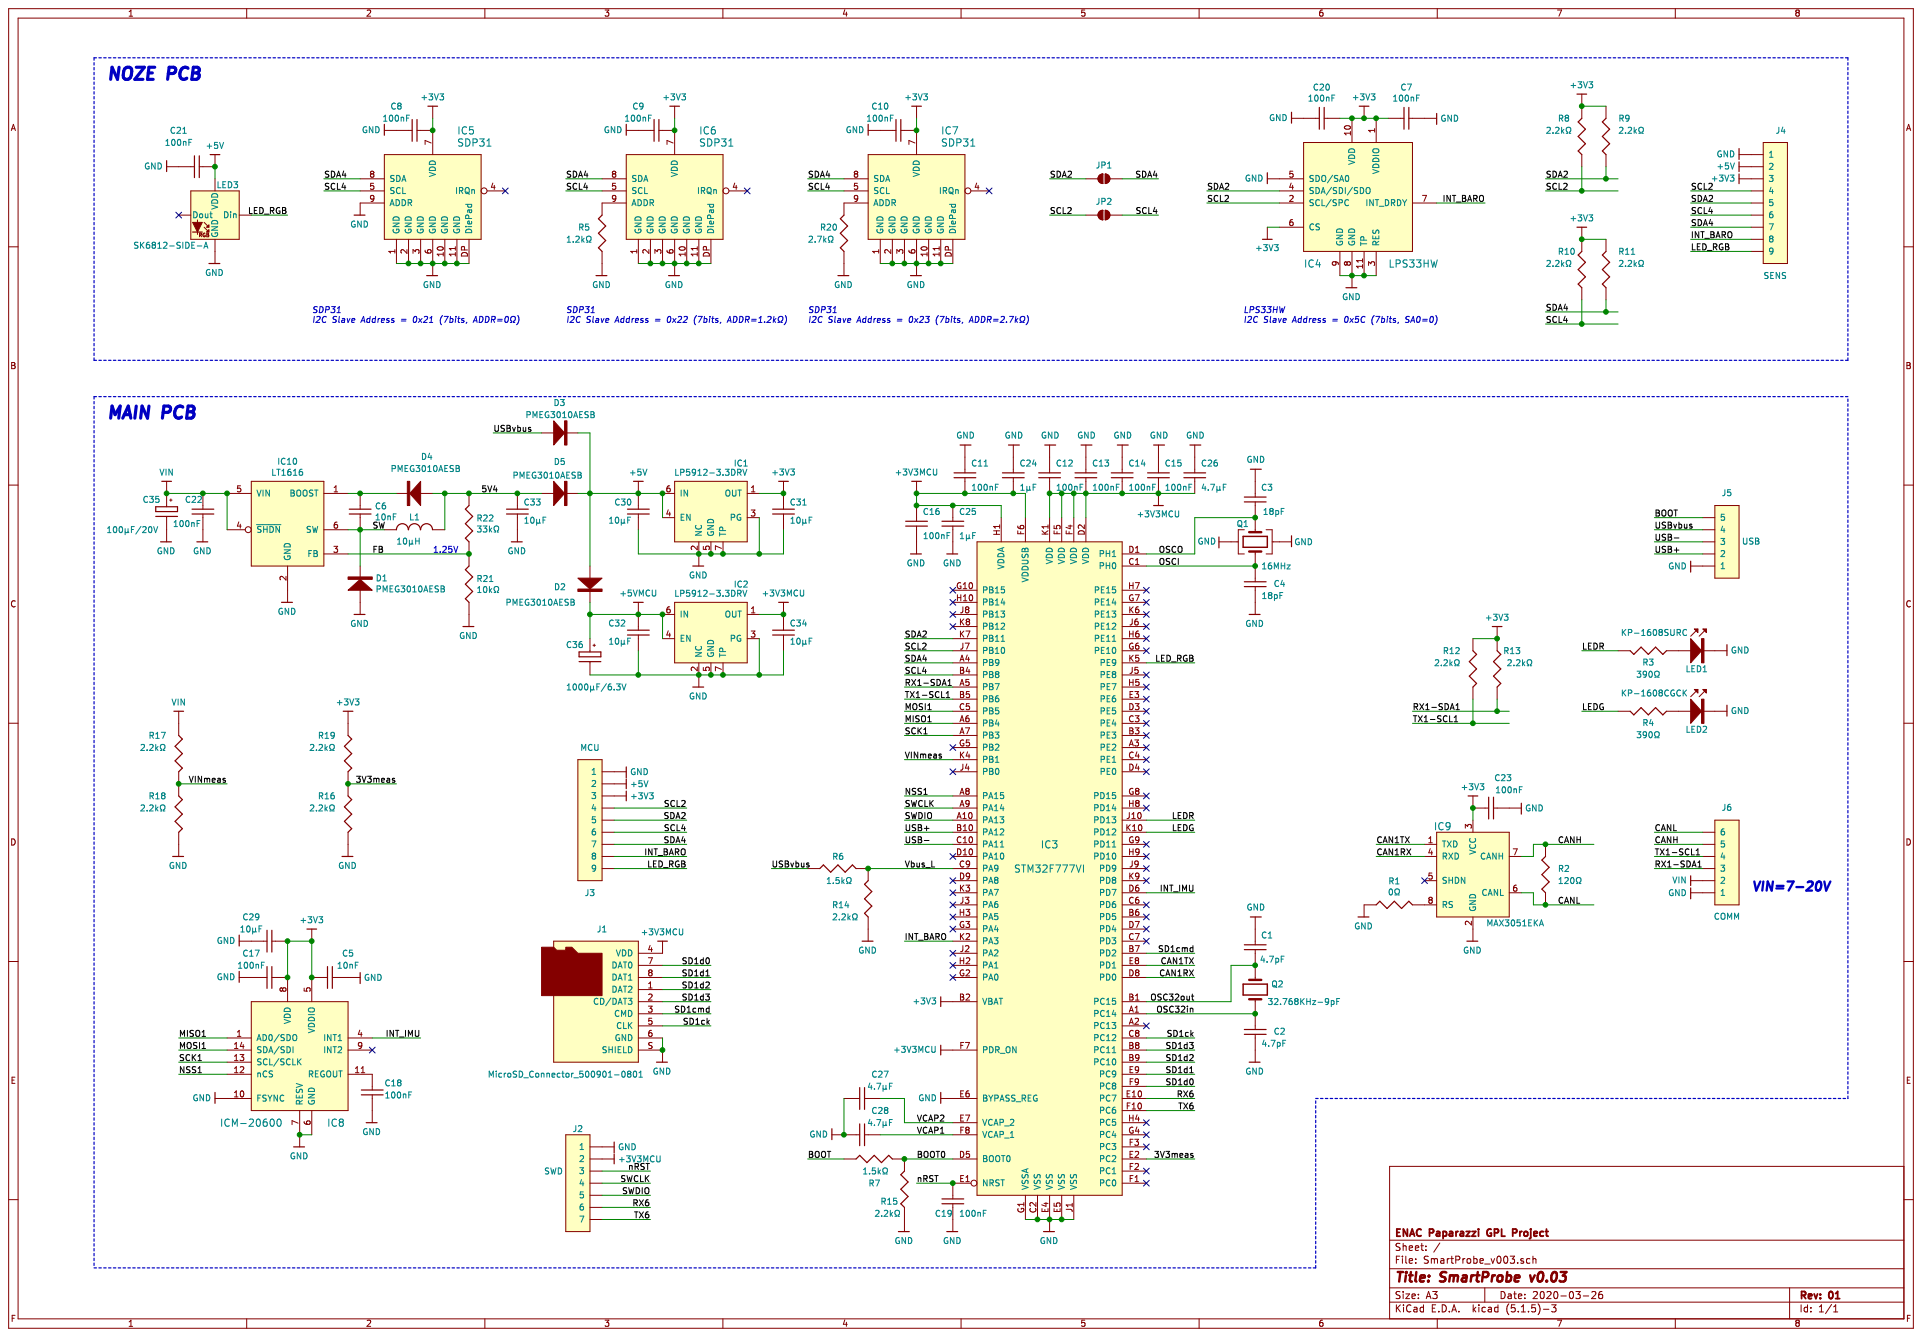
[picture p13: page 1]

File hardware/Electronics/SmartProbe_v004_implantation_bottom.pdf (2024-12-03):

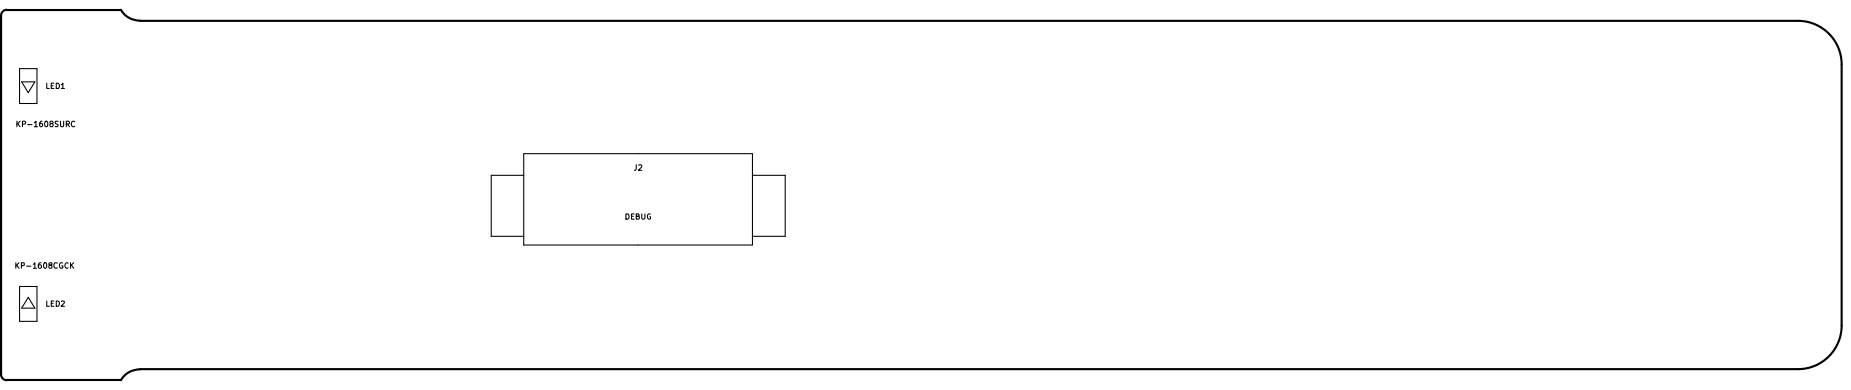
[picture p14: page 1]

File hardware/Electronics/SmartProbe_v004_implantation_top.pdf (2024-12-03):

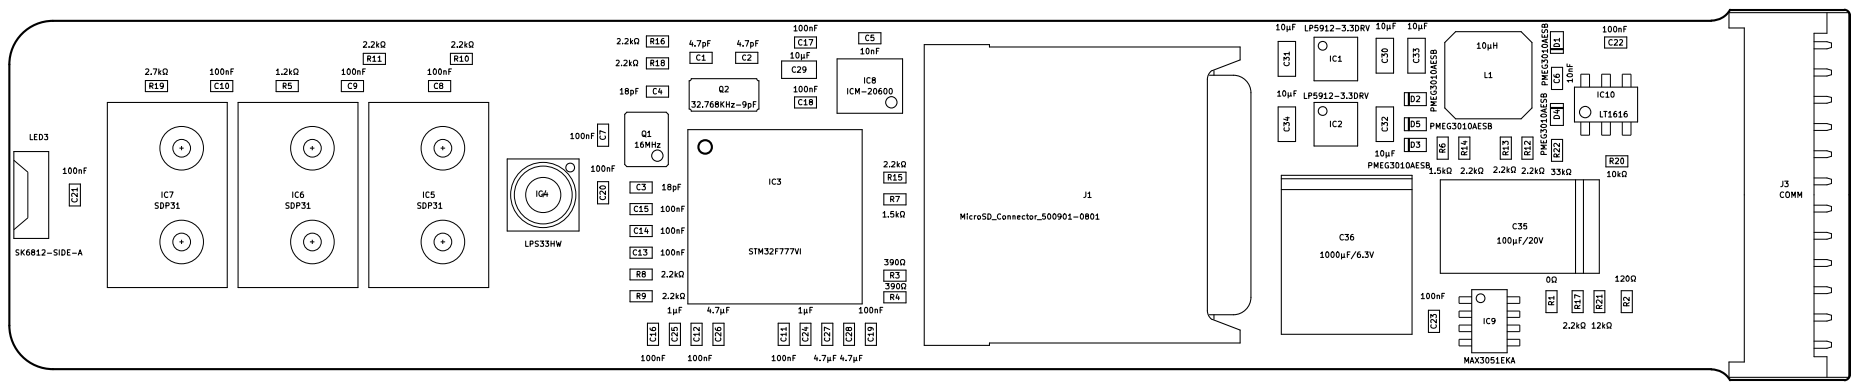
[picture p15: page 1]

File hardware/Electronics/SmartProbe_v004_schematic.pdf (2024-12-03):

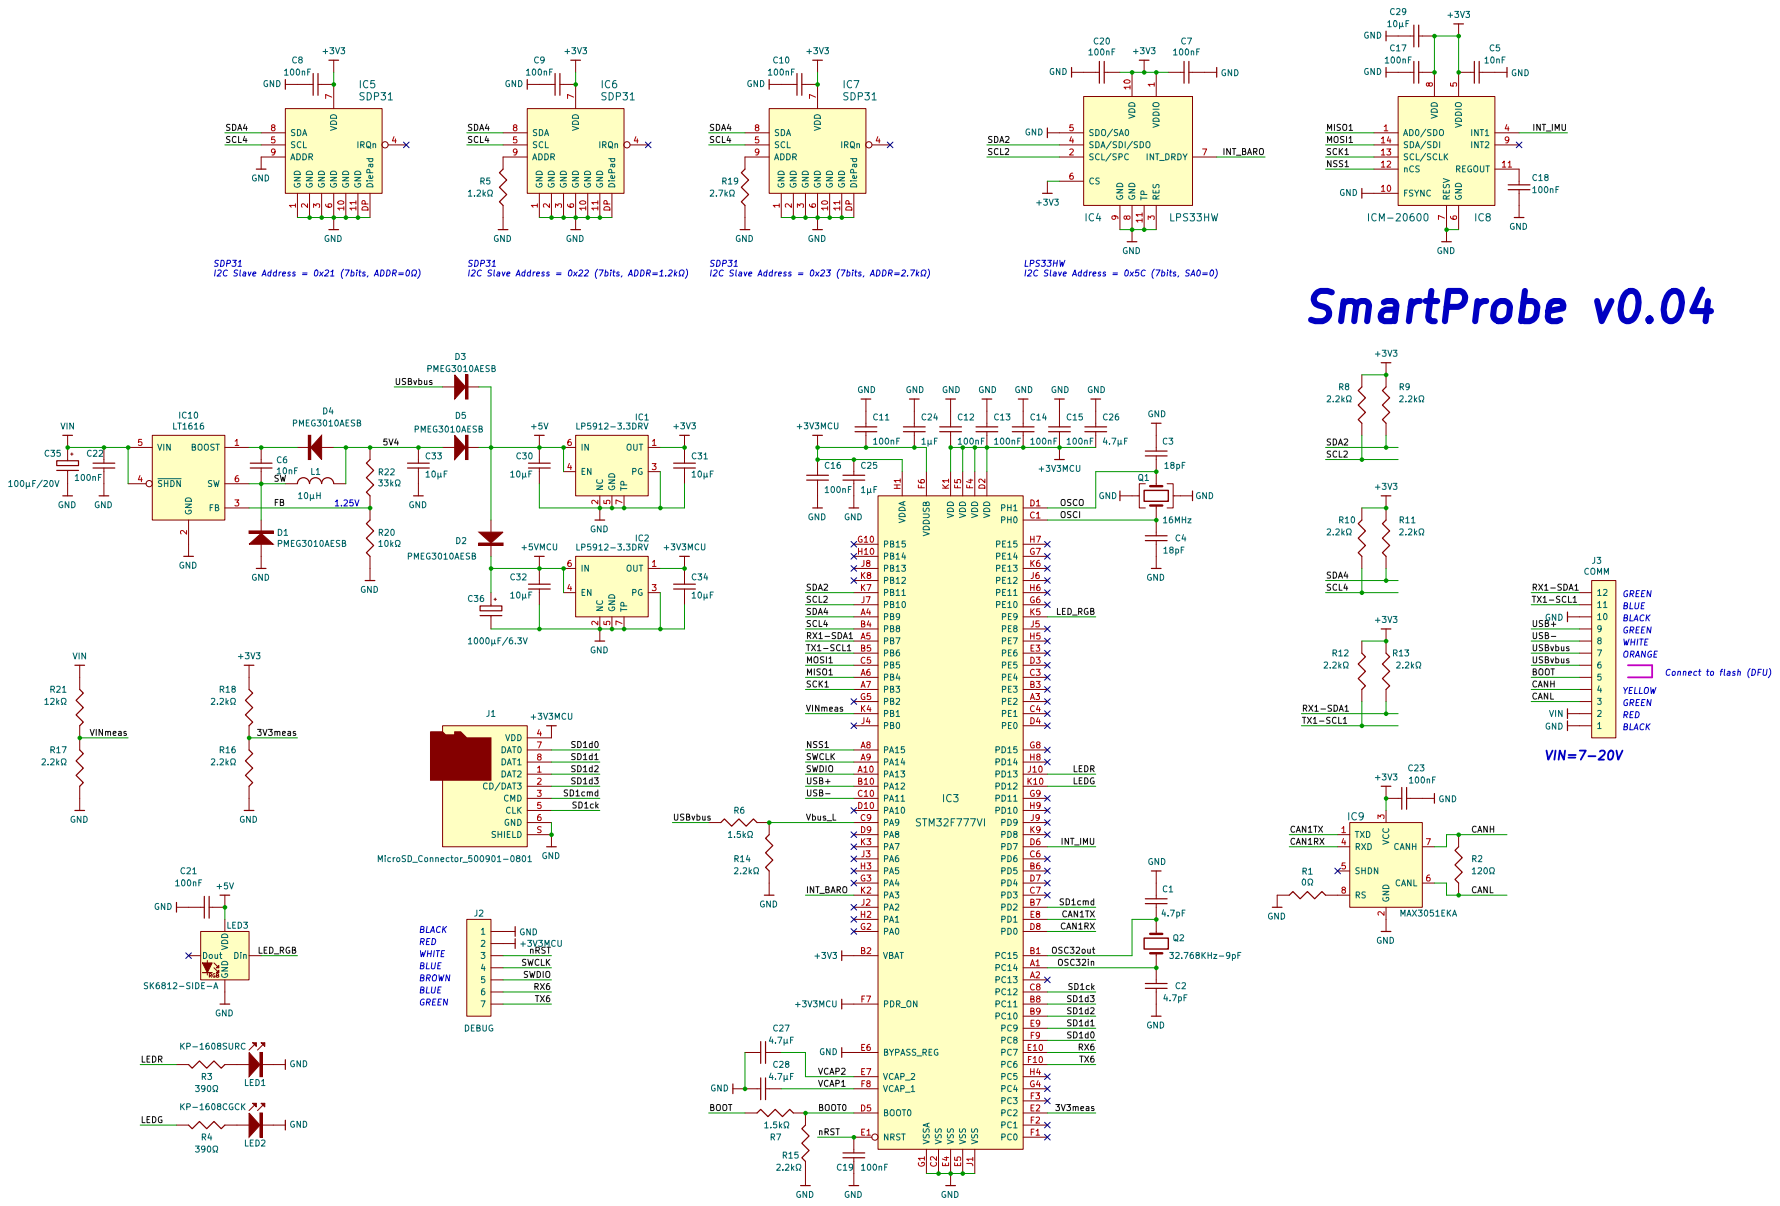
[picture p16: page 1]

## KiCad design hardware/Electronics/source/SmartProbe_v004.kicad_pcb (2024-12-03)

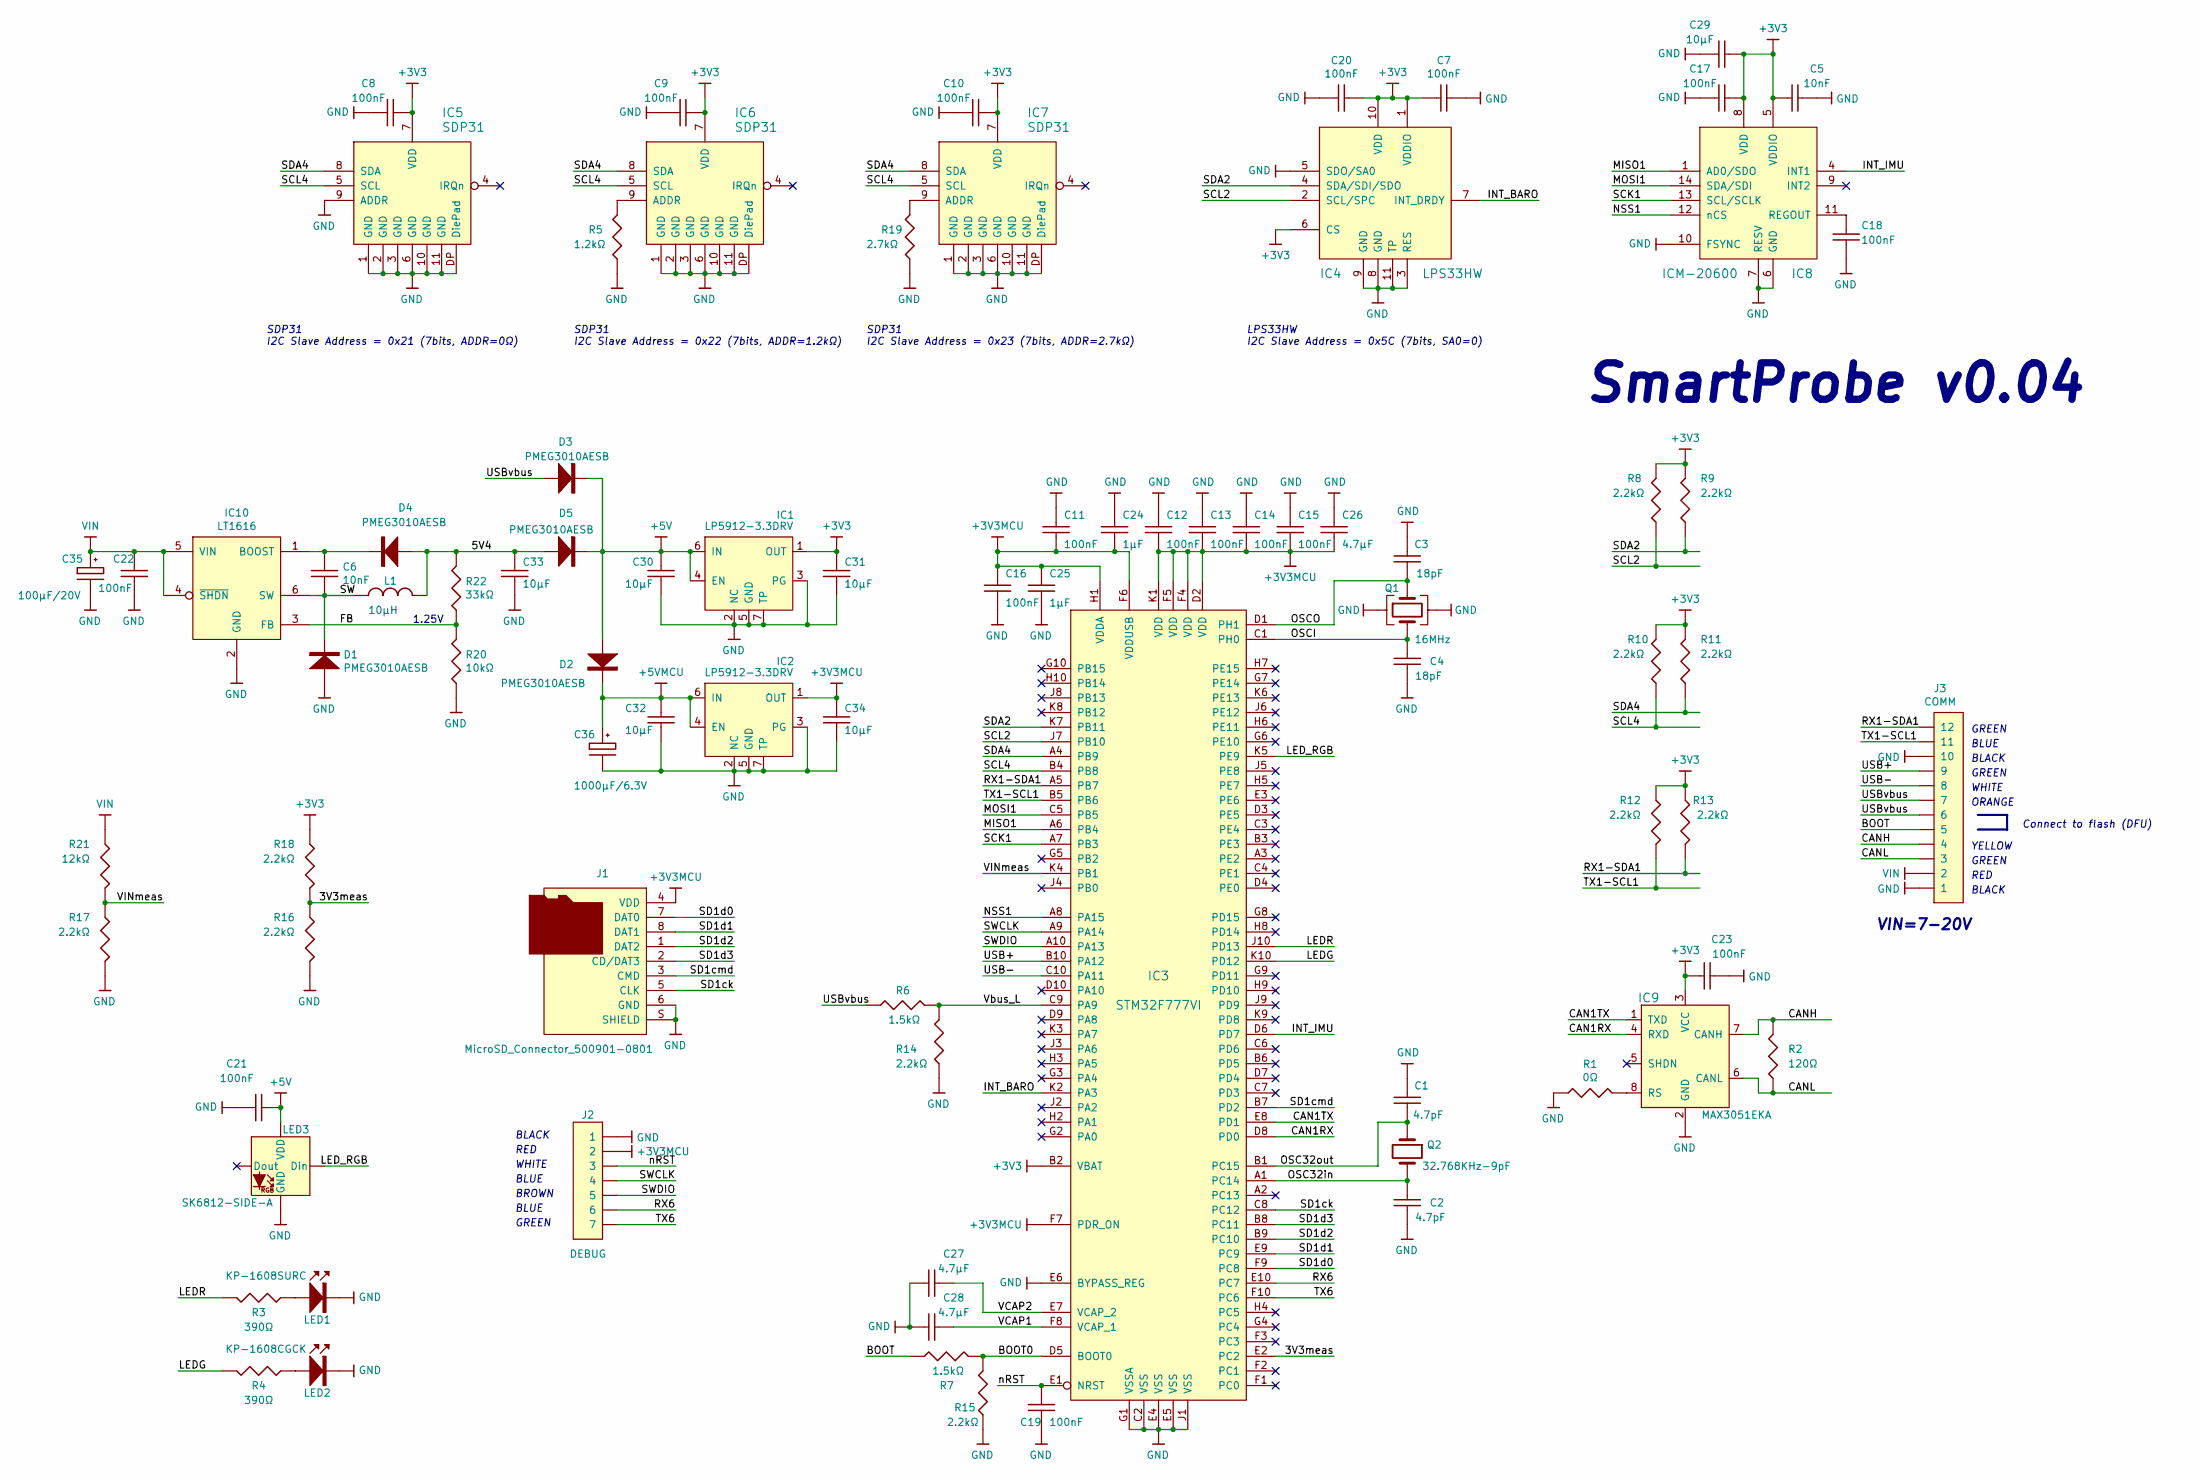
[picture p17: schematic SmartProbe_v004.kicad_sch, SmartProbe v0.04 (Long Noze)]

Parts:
C1, C2: 4.7pF; C_0402
C3, C4: 18pF; C_0402
C5, C6: 10nF; C_0402
C7, C8, C9, C10, C11, C12, C13, C14, C15, C16, C17, C18, C19, C20, C21, C22, C23: 100nF; C_0402
C24, C25: 1µF; C_0402
C26, C27, C28: 4.7µF; C_0402
C29, C30, C31, C32, C33, C34: 10µF; C_0603
C35: 100µF/20V; EIA_7343-31
C36: 1000µF/6.3V; EIA_7360-38
D1, D2, D3, D4, D5: PMEG3010AESB
IC1, IC2: LP5912-3.3DRV; LP5912DRV
IC3: STM32F777VI
IC4: LPS33HW
IC5, IC6, IC7: SDP31
IC8: ICM-20600
IC9: MAX3051EKA
IC10: LT1616
J1: MicroSD_Connector_500901-0801; MicroSD_500901-0801
J2: DEBUG; PicoBlade_53261-0771
J3: COMM; PicoBlade_53048-1210
L1: 10µH; VLCF4020T
LED1: KP-1608SURC
LED2: KP-1608CGCK
LED3: SK6812-SIDE-A
Q1: 16MHz; Crystal_8Z
Q2: 32.768KHz-9pF; Crystal_FC-135
R1: 0Ω; R_0402
R2: 120Ω; R_0402
R3, R4: 390Ω; R_0402
R5: 1.2kΩ; R_0402
R6, R7: 1.5kΩ; R_0402
R8, R9, R10, R11, R12, R13, R14, R15, R16, R17, R18: 2.2kΩ; R_0402
R19: 2.7kΩ; R_0402
R20: 10kΩ; R_0402
R21: 12kΩ; R_0402
R22: 33kΩ; R_0402

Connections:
+3V3: C5.2, C7.2, C8.1, C9.1, C10.1, C17.1, C20.1, C23.2, C29.1, C31.1, IC1.1 (OUT), IC3.B2 (VBAT), IC4.1 (VDDIO), IC4.6 (CS), IC4.10 (VDD), IC5.7 (VDD), IC6.7 (VDD), IC7.7 (VDD), IC8.5 (VDDIO), IC8.8 (VDD), IC9.3 (VCC), R8.1, R9.1, R10.1, R11.1, R12.1, R13.1, R18.1
+3V3MCU: C11.2, C12.2, C13.2, C14.2, C15.2, C16.1, C24.2, C25.1, C26.2, C34.1, IC2.1 (OUT), IC3.D2 (VDD), IC3.F4 (VDD), IC3.F5 (VDD), IC3.F6 (VDDUSB), IC3.F7 (PDR_ON), IC3.H1 (VDDA), IC3.K1 (VDD), J1.4 (VDD), J2.2
+5V: C21.1, C30.1, D2.2 (A), D3.1 (K), D5.1 (K), IC1.4 (EN), IC1.6 (IN), LED3.2 (VDD)
+5VMCU: C32.1, C36.1, D2.1 (K), IC2.4 (EN), IC2.6 (IN)
/3V3meas: IC3.E2 (PC2), R16.1, R18.2
/5V4: C33.1, D4.2 (A), D5.2 (A), L1.2, R22.1
/BOOT: J3.5, R7.2
/BOOT0: IC3.D5 (BOOT0), R7.1, R15.1
/CAN1RX: IC3.D8 (PD0), IC9.4 (RXD)
/CAN1TX: IC3.E8 (PD1), IC9.1 (TXD)
/CANH: IC9.7 (CANH), J3.4, R2.1
/CANL: IC9.6 (CANL), J3.3, R2.2
/FB: IC10.3 (FB), R20.1, R22.2
/INT_BARO: IC3.K2 (PA3), IC4.7 (INT_DRDY)
/INT_IMU: IC3.D6 (PD7), IC8.4 (INT1)
/LEDG: IC3.K10 (PD12), R4.1
/LEDR: IC3.J10 (PD13), R3.1
/LED_RGB: IC3.K5 (PE9), LED3.1 (Din)
/MISO1: IC3.A6 (PB4), IC8.1 (AD0/SDO)
/MOSI1: IC3.C5 (PB5), IC8.14 (SDA/SDI)
/NSS1: IC3.A8 (PA15), IC8.12 (nCS)
/OSC32in: C2.2, IC3.A1 (PC14), Q2.2
/OSC32out: C1.2, IC3.B1 (PC15), Q2.1
/OSCI: C4.2, IC3.C1 (PH0), Q1.3
/OSCO: C3.2, IC3.D1 (PH1), Q1.1
/RX1-SDA1: IC3.A5 (PB7), J3.12, R13.2
/RX6: IC3.E10 (PC7), J2.6
/SCK1: IC3.A7 (PB3), IC8.13 (SCL/SCLK)
/SCL2: IC3.J7 (PB10), IC4.2 (SCL/SPC), R8.2
/SCL4: IC3.B4 (PB8), IC5.5 (SCL), IC6.5 (SCL), IC7.5 (SCL), R10.2
/SD1ck: IC3.C8 (PC12), J1.5 (CLK)
/SD1cmd: IC3.B7 (PD2), J1.3 (CMD)
/SD1d0: IC3.F9 (PC8), J1.7 (DAT0)
/SD1d1: IC3.E9 (PC9), J1.8 (DAT1)
/SD1d2: IC3.B9 (PC10), J1.1 (DAT2)
/SD1d3: IC3.B8 (PC11), J1.2 (CD/DAT3)
/SDA2: IC3.K7 (PB11), IC4.4 (SDA/SDI/SDO), R9.2
/SDA4: IC3.A4 (PB9), IC5.8 (SDA), IC6.8 (SDA), IC7.8 (SDA), R11.2
/SW: C6.2, D1.1 (K), IC10.6 (SW), L1.1
/SWCLK: IC3.A9 (PA14), J2.4
/SWDIO: IC3.A10 (PA13), J2.5
/TX1-SCL1: IC3.B5 (PB6), J3.11, R12.2
/TX6: IC3.F10 (PC6), J2.7
/USB+: IC3.B10 (PA12), J3.9
/USB-: IC3.C10 (PA11), J3.8
/USBvbus: D3.2 (A), J3.6, J3.7, R6.2
/VCAP1: C28.1, IC3.F8 (VCAP_1)
/VCAP2: C27.1, IC3.E7 (VCAP_2)
/VINmeas: IC3.K4 (PB1), R17.1, R21.2
/Vbus_L: IC3.C9 (PA9), R6.1, R14.1
/nRST: C19.1, IC3.E1 (NRST), J2.3
GND: C1.1, C2.1, C3.1, C4.1, C5.1, C7.1, C8.2, C9.2, C10.2, C11.1, C12.1, C13.1, C14.1, C15.1, C16.2, C17.2, C18.2, C19.2, C20.2, C21.2, C22.2, C23.1, C24.1, C25.2, C26.1, C27.2, C28.2, C29.2, C30.2, C31.2, C32.2, C33.2, C34.2, C35.2, C36.2, D1.2 (A), IC1.2 (NC), IC1.3 (PG), IC1.5 (GND), IC1.7 (TP), IC2.2 (NC), IC2.3 (PG), IC2.5 (GND), IC2.7 (TP), IC3.C2 (VSS), IC3.E4 (VSS), IC3.E5 (VSS), IC3.E6 (BYPASS_REG), IC3.G1 (VSSA), IC3.J1 (VSS), IC4.3 (RES), IC4.5 (SDO/SA0), IC4.8 (GND), IC4.9 (GND), IC4.11 (TP), IC5.1 (GND), IC5.2 (GND), IC5.3 (GND), IC5.6 (GND), IC5.9 (ADDR), IC5.10 (GND), IC5.11 (GND), IC5.DP (DiePad), IC6.1 (GND), IC6.2 (GND), IC6.3 (GND), IC6.6 (GND), IC6.10 (GND), IC6.11 (GND), IC6.DP (DiePad), IC7.1 (GND), IC7.2 (GND), IC7.3 (GND), IC7.6 (GND), IC7.10 (GND), IC7.11 (GND), IC7.DP (DiePad), IC8.6 (GND), IC8.7 (RESV), IC8.10 (FSYNC), IC9.2 (GND), IC10.2 (GND), J1.6 (GND), J1.S (SHIELD), J2.1, J3.1, J3.10, LED1.1 (K), LED2.1 (K), LED3.4 (GND), Q1.2, Q1.4, R1.2, R5.2, R14.2, R15.2, R16.2, R17.2, R19.2, R20.2
unnamed: C6.1, D4.1 (K), IC10.1 (BOOST)
unnamed: C18.1, IC8.11 (REGOUT)
unnamed: IC6.9 (ADDR), R5.1
unnamed: IC7.9 (ADDR), R19.1
unnamed: IC9.8 (RS), R1.1
unnamed: LED1.2 (A), R3.2
unnamed: LED2.2 (A), R4.2
VIN: C22.1, C35.1, IC10.4 (~SHDN), IC10.5 (VIN), J3.2, R21.1

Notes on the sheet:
GREEN
BLACK
1.25V
ORANGE
BROWN
BLUE
WHITE
SDP31 I2C Slave Address = 0x22 (7bits, ADDR=1.2kΩ)
SDP31 I2C Slave Address = 0x21 (7bits, ADDR=0Ω)
VIN=7-20V
YELLOW
RED
LPS33HW I2C Slave Address = 0x5C (7bits, SA0=0)
SmartProbe v0.04
Connect to flash (DFU)
SDP31 I2C Slave Address = 0x23 (7bits, ADDR=2.7kΩ)

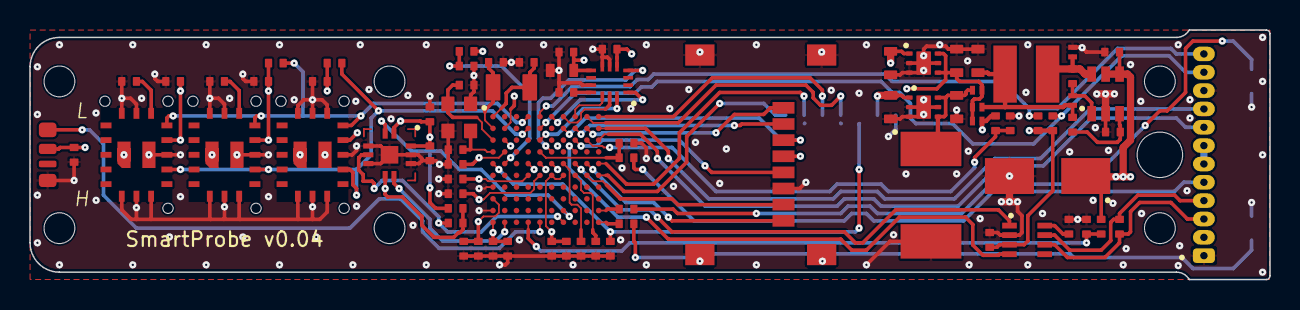
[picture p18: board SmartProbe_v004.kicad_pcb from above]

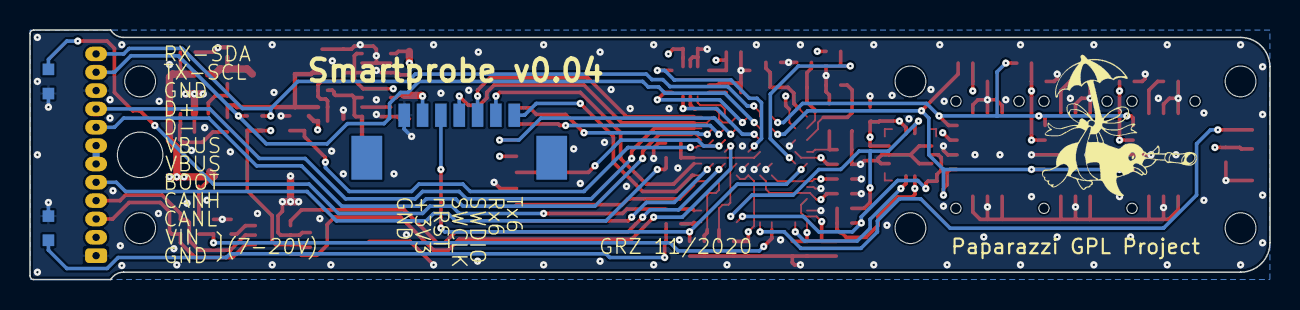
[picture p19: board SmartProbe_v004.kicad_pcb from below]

Board: 4 copper layers, 84.5 x 17.0 mm, 82 parts (3 on the bottom side), 60 nets.

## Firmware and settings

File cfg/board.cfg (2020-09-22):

MCU_MODEL = STM32F777VIHx
CHIBIOS_VERSION = 3.0

HEADER
/*
 * Board identifier.
 */
#define BOARD_NAME                  "SmartProbe Drones@ENAC"

/*
 * Board oscillators-related settings.
 */
#if !defined(STM32_LSECLK)
#define STM32_LSECLK                32768U
#endif

#define STM32_LSEDRV                (3U << 3U)

#if !defined(STM32_HSECLK)
#define STM32_HSECLK                16000000U
#endif

/*
 * Board voltages.
 * Required for performance limits calculation.
 */
#define STM32_VDD                   300U

/*
 * MCU type as defined in the ST header.
 */
#define STM32F767xx


CONFIG
# PIN NAME PERIPH_TYPE AF_NUMBER or
# PIN NAME FUNCTION PP_or_OPENDRAIN PIN_SPEED PULL_RESISTOR INITIAL_LEVEL AF_NUMBER
# SPEED : SPEED_VERYLOW,  SPEED_LOW,  SPEED_MEDIUM,  SPEED_HIGH
#
# DEFAULT AND SYS
A13 	SWDIO     SYS  AF:SYS_JTMS-SWDIO
A14 	SWCLK     SYS  AF:SYS_JTCK-SWCLK
C14 	OSC32_IN  OSC  
C15 	OSC32_OUT OSC  
H00 	OSC_IN    OSC  
H01 	OSC_OUT   OSC  

DEFAULT INPUT PUSHPULL SPEED_VERYLOW PULLDOWN LEVEL_LOW AF0


# ACTIVE PINS
PA03     BARO_DRDY      INPUT		PULLUP	3_3VOLTS
PA09     USB_VBUS	INPUT		PULLDOWN
PA11     USB_DM		OTG		AF:USB_OTG_FS_DM
PA12     USB_DP		OTG		AF:USB_OTG_FS_DP   
PA15     SPI1_NSS	OUTPUT		PUSHPULL

PB01     POWSUPLY_MEAS	ADC		ADC1_IN9
PB03     IMU_SPI_SCK1	SPI		AF:SPI1_SCK       
PB04     IMU_SPI_MISO1	SPI		AF:SPI1_MISO
PB05     IMU_SPI_MOSI1	SPI		AF:SPI1_MOSI	
PB06     AP_TX1		UART		AF:USART1_TX
PB07     AP_RX1		UART		AF:USART1_RX
PB08     PRESS_SCL4	I2C		AF:I2C4_SCL        
PB09     PRESS_SDA4	I2C		AF:I2C4_SDA        
PB10     BARO_SCL2	I2C		AF:I2C2_SCL        
PB11     BARO_SDA2	I2C		AF:I2C2_SDA        

PC02	 V3V_MEAS	ADC		ADC1_IN12
PC06     DBG_TX6	UART		AF:USART6_TX
PC07     DBG_RX6	UART		AF:USART6_RX
PC08     SDMMC1_D0      SDIO		AF:SDMMC1_D0 
PC09     SDMMC1_D1      SDIO		AF:SDMMC1_D1
PC10     SDMMC1_D2      SDIO 		AF:SDMMC1_D2
PC11     SDMMC1_D3      SDIO 		AF:SDMMC1_D3
PC12     SDMMC1_CK      SDIO 		AF:SDMMC1_CK

PD00     CAN1_RX        CAN		AF:CAN1_RX 
PD01     CAN1_TX        CAN		AF:CAN1_TX 
PD02     SDMMC1_CMD     SDIO		AF:SDMMC1_CMD
PD07     IMU_INT1       INPUT		FLOATING

PD12     LED_GREEN	LED		PUSHPULL SPEED_VERYLOW  LEVEL_LOW
PD13     LED_RED	LED		PUSHPULL SPEED_VERYLOW  LEVEL_LOW

PE09	 LED_RGB	PWM		AF:TIM1_CH1

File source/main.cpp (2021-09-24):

#include <ch.h>
#include <hal.h>
#include <cstdio>
#include "stdutil.h"
#include "cpp_heap_alloc.hpp"
#include "ttyConsole.hpp"       
#include "confFile.hpp"
#include "workerClass.hpp"
#include "threadAndEventDecl.hpp"
//#include "blinker.hpp"
#include "usbStorage.hpp"
#include "dynSwdio.hpp"
#include "transmitPprzlink.hpp"
#include "receivePprzlink.hpp"
#include "receiveNmealink.hpp"
#include "rtcSync.hpp"
#include "healthCheck.hpp"
#include "util.hpp"
#include "printf.h"



/*
  Câbler une LED sur la broche C0


  ° connecter B6 (uart1_tx) sur PROBE+SERIAL Rx AVEC UN JUMPER
  ° connecter B7 (uart1_rx) sur PROBE+SERIAL Tx AVEC UN JUMPER
  ° connecter C0 sur led0

 */


void _init_chibios() __attribute__ ((constructor(101)));
void _init_chibios() {
  halInit();
  chSysInit();
  initHeap ();
}

extern FrontLed IN_DMA_SECTION(fl);

int main (void)
{
  //  Blinker       bl(NORMALPRIO+1);
  UsbStorage    usbStorage(NORMALPRIO);
  DynSwdio	dynSwdio(NORMALPRIO);
  TransmitPprzlink transmitPPL(NORMALPRIO);
  RtcSync	rtcSync(NORMALPRIO);
  HealthCheck   healthCheck(NORMALPRIO-1);
  
  fl.setError(LedCode::Starting);

  //  bl.run(TIME_MS2I(1000));
  
#ifdef TRACE
  consoleInit();    // initialisation des objets liés au shell
  consoleLaunch();  // lancement du shell
#endif

  // first time without loggin error to get early parameters
  if (not sdcard.initHardware()) {
    DebugTrace("sdcard.initHardware() has failed");
    fl.setError(LedCode::NoSdCard);
  } else if (not confFile.earlyReadConfFile()) {
    DebugTrace("early confFile.readConfFile() has failed");
    fl.setError(LedCode::ConfigError);
  } else if (not sdcard.run(TIME_IMMEDIATE)) {
    chprintf(chp, "SDCARD launch fail");
    fl.setError(LedCode::NoSdCard);
  } else if (chThdSleepMilliseconds(300); not confFile.populate()) { // second time to log errors
    chprintf(chp, "read CONFIGURATION file fail");
    fl.setError(LedCode::ConfigError);
  } else if (not baro.run(TIME_IMMEDIATE)) {
    SdCard::logSyslog(Severity::Fatal, "BARO fail");
    fl.setError(LedCode::HardFault);
  } else  if (not dp.run(PERIOD("thread.frequency.d_press"))) {
    SdCard::logSyslog(Severity::Fatal, "DIFF PRESS fail");
    fl.setError(LedCode::HardFault);
   } else if (not imu.run(PERIOD("thread.frequency.imu"))) {
     SdCard::logSyslog(Severity::Fatal, "IMU fail");
    fl.setError(LedCode::HardFault);
   } else if (not ahrs.run(TIME_IMMEDIATE)) {
     SdCard::logSyslog(Severity::Fatal, "Ahrs fail");
    fl.setError(LedCode::HardFault);
   } else if (not relwind.run(TIME_IMMEDIATE)) {
     SdCard::logSyslog(Severity::Fatal, "relative wind fail");
    fl.setError(LedCode::HardFault);
   } else if (not usbStorage.run(TIME_IMMEDIATE)) {
     SdCard::logSyslog(Severity::Fatal, "USB Storage fail");
    fl.setError(LedCode::HardFault);
   } else if (not adc.run(TIME_IMMEDIATE)) {
     SdCard::logSyslog(Severity::Fatal, "ADC fail");
    fl.setError(LedCode::HardFault);
  } else if (not dynSwdio.run(TIME_IMMEDIATE)) {
     SdCard::logSyslog(Severity::Fatal, "dynSwdio fail");
    fl.setError(LedCode::HardFault);
  } else if (not healthCheck.run(TIME_S2I(1))) { // check internal voltage, thread memory, cpu usage
     SdCard::logSyslog(Severity::Fatal, "healthCheck fail");
    fl.setError(LedCode::HardFault);
  } else if (not rtcSync.run(TIME_S2I(60))) { // sync rtc with gps every minutes
     SdCard::logSyslog(Severity::Fatal, "rtcSync fail");
    fl.setError(LedCode::HardFault);
  } else {
#ifdef TRACE
    if (not showBB.run(TIME_IMMEDIATE)) {
      SdCard::logSyslog(Severity::Fatal, "Show Blackboard fail");
      fl.setError(LedCode::HardFault);
    } 
#endif
    const SerialMode smode = static_cast<SerialMode>(CONF("uart.mode"));
    switch (smode) {
    case SERIAL_NOT_USED :
      SdCard::logSyslog(Severity::Warning, "mode serial line NOT USED");
      break;
    case PPRZ_IN_OUT:
      transmitPPL.run(TIME_IMMEDIATE);
      receivePPL.run(TIME_IMMEDIATE);
      break;
    case NMEA_IN:
     receiveNMEA.run(TIME_IMMEDIATE);
      break;
    case UBX_IN:
      receiveUBX.run(TIME_IMMEDIATE);
      break;
    }
    const LedMode ledmode = static_cast<LedMode>(CONF("led.mode"));
    if (ledmode == LED_STATUS) {
      // if all went ok, main thead now can rest
      fl.setError(LedCode::Optimal);
    } else {
      // demo mode where led reflect 3D airspeed measures
      fl.setError(LedCode::DirectColorSetting);
      demoled.run(TIME_MS2I(30));
    }
    chThdSleep(TIME_INFINITE);
  }

  // if something goes wrong, control finish here
  // still offer usb storage facility, so in case of configuration file
  // error, one can still mount the device to read syslog and fix conf file
  palSetLine(LINE_LED_RED);
  usbStorage.setModeEmergency();
  usbStorage.run(TIME_IMMEDIATE);
  chThdSleep(TIME_INFINITE);
}

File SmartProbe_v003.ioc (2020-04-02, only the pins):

Mcu.UserName=STM32F777VIHx
PA11.GPIO_Label=USB-
PA11.Signal=USB_OTG_FS_DM
PA12.GPIO_Label=USB+
PA12.Signal=USB_OTG_FS_DP
PA13.GPIO_Label=SWDIO
PA13.Signal=SYS_JTMS-SWDIO
PA14.GPIO_Label=SWCLK
PA14.Signal=SYS_JTCK-SWCLK
PA15.GPIO_Label=NSS1
PA15.Signal=SPI1_NSS
PA3.GPIO_Label=INT_BARO
PA3.Signal=GPIO_Input
PA9.GPIO_Label=Vbus
PA9.Signal=USB_OTG_FS_VBUS
PB1.GPIO_Label=VINmeas
PB1.Signal=ADCx_IN9
PB10.GPIO_Label=SCL2
PB10.Signal=I2C2_SCL
PB11.GPIO_Label=SDA2
PB11.Signal=I2C2_SDA
PB3.GPIO_Label=SCK1
PB3.Signal=SPI1_SCK
PB4.GPIO_Label=MISO1
PB4.Signal=SPI1_MISO
PB5.GPIO_Label=MOSI1
PB5.Signal=SPI1_MOSI
PB6.GPIO_Label=TX1-SCL1
PB6.Signal=USART1_TX
PB7.GPIO_Label=RX1-SDA1
PB7.Signal=USART1_RX
PB8.GPIO_Label=SCL4
PB8.Signal=I2C4_SCL
PB9.GPIO_Label=SDA4
PB9.Signal=I2C4_SDA
PC10.GPIO_Label=SD1d2
PC10.Signal=SDMMC1_D2
PC11.GPIO_Label=SD1d3
PC11.Signal=SDMMC1_D3
PC12.GPIO_Label=SD1ck
PC12.Signal=SDMMC1_CK
PC14/OSC32_IN.GPIO_Label=OSC32IN
PC14/OSC32_IN.Signal=RCC_OSC32_IN
PC15/OSC32_OUT.GPIO_Label=OSC32OUT
PC15/OSC32_OUT.Signal=RCC_OSC32_OUT
PC2.GPIO_Label=_3V3meas
PC2.Signal=ADCx_IN12
PC6.GPIO_Label=TX6
PC6.Signal=USART6_TX
PC7.GPIO_Label=RX6
PC7.Signal=USART6_RX
PC8.GPIO_Label=SD1d0
PC8.Signal=SDMMC1_D0
PC9.GPIO_Label=SD1d1
PC9.Signal=SDMMC1_D1
PD0.GPIO_Label=CAN1RX
PD0.Signal=CAN1_RX
PD1.GPIO_Label=CAN1TTX
PD1.Signal=CAN1_TX
PD12.GPIO_Label=LEDG
PD12.Signal=GPIO_Output
PD13.GPIO_Label=LEDR
PD13.Signal=GPIO_Output
PD2.GPIO_Label=SD1cmd
PD2.Signal=SDMMC1_CMD
PD7.GPIO_Label=INT_IMU
PD7.Signal=GPIO_Input
PE9.GPIO_Label=LED_RGB
PE9.Signal=S_TIM1_CH1
PH0/OSC_IN.Signal=RCC_OSC_IN
PH1/OSC_OUT.Signal=RCC_OSC_OUT

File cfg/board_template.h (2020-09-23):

/*
    ChibiOS - Copyright (C) 2006..2015 Giovanni Di Sirio

    Licensed under the Apache License, Version 2.0 (the "License");
    you may not use this file except in compliance with the License.
    You may obtain a copy of the License at

        http://www.apache.org/licenses/LICENSE-2.0

    Unless required by applicable law or agreed to in writing, software
    distributed under the License is distributed on an "AS IS" BASIS,
    WITHOUT WARRANTIES OR CONDITIONS OF ANY KIND, either express or implied.
    See the License for the specific language governing permissions and
    limitations under the License.
*/

#pragma once

/*
 * Board identifier.
 */
#define BOARD_NAME                  "SmartProbe Drones@ENAC"

/*
 * Board oscillators-related settings.
 */
#if !defined(STM32_LSECLK)
#define STM32_LSECLK                32768U
#endif

#define STM32_LSEDRV                (3U << 3U)

#if !defined(STM32_HSECLK)
#define STM32_HSECLK                16000000U
#endif

/*
 * Board voltages.
 * Required for performance limits calculation.
 */
#define STM32_VDD                   300U

/*
 * MCU type as defined in the ST header.
 */
#define STM32F767xx


/*
 * IO pins assignments.
 */
#define	PA00                           0U
#define	PA01                           1U
#define	PA02                           2U
#define	PA03_BARO_DRDY                 3U
#define	PA04                           4U
#define	PA05                           5U
#define	PA06                           6U
#define	PA07                           7U
#define	PA08                           8U
#define	PA09_USB_VBUS                  9U
#define	PA10                           10U
#define	PA11_USB_DM                    11U
#define	PA12_USB_DP                    12U
#define	PA13_SWDIO                     13U
#define	PA14_SWCLK                     14U
#define	PA15_SPI1_NSS                  15U

#define	PB00                           0U
#define	PB01_POWSUPLY_MEAS             1U
#define	PB02                           2U
#define	PB03_IMU_SPI_SCK1              3U
#define	PB04_IMU_SPI_MISO1             4U
#define	PB05_IMU_SPI_MOSI1             5U
#define	PB06_AP_TX1                    6U
#define	PB07_AP_RX1                    7U
#define	PB08_PRESS_SCL4                8U
#define	PB09_PRESS_SDA4                9U
#define	PB10_BARO_SCL2                 10U
#define	PB11_BARO_SDA2                 11U
#define	PB12                           12U
#define	PB13                           13U
#define	PB14                           14U
#define	PB15                           15U

#define	PC00                           0U
#define	PC01                           1U
#define	PC02_V3V_MEAS                  2U
#define	PC03                           3U
#define	PC04                           4U
#define	PC05                           5U
#define	PC06_DBG_TX6                   6U
#define	PC07_DBG_RX6                   7U
#define	PC08_SDMMC1_D0                 8U
#define	PC09_SDMMC1_D1                 9U
#define	PC10_SDMMC1_D2                 10U
#define	PC11_SDMMC1_D3                 11U
#define	PC12_SDMMC1_CK                 12U
#define	PC13                           13U
#define	PC14_OSC32_IN                  14U
#define	PC15_OSC32_OUT                 15U

#define	PD00_CAN1_RX                   0U
#define	PD01_CAN1_TX                   1U
#define	PD02_SDMMC1_CMD                2U
#define	PD03                           3U
#define	PD04                           4U
#define	PD05                           5U
#define	PD06                           6U
#define	PD07_IMU_INT1                  7U
#define	PD08                           8U
#define	PD09                           9U
#define	PD10                           10U
#define	PD11                           11U
#define	PD12_LED_GREEN                 12U
#define	PD13_LED_RED                   13U
#define	PD14                           14U
#define	PD15                           15U

#define	PE00                           0U
#define	PE01                           1U
#define	PE02                           2U
#define	PE03                           3U
#define	PE04                           4U
#define	PE05                           5U
#define	PE06                           6U
#define	PE07                           7U
#define	PE08                           8U
#define	PE09_LED_RGB                   9U
#define	PE10                           10U
#define	PE11                           11U
#define	PE12                           12U
#define	PE13                           13U
#define	PE14                           14U
#define	PE15                           15U
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

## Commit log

2019-10-25 smartprobe : board.cfg written for specific hardware
    [board.cfg]
2019-11-08 add fatfs, tlsf
    [board.cfg]
2019-11-15 add i2cMaster, spi; fix dma streams
    [halconf.h, hardwareConf.hpp, main.cpp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]
2019-11-15 add baro thread
2019-11-15 add missing baro files
    [barometer.cpp]
2019-11-18 fix thread abstaction, before baro using thread abstaction, tested ok on devboardm767
    [barometer.cpp, differentialPressure.cpp, main.cpp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]
2019-11-19 baro use thread abstraction
2019-11-19 add adc, apply CRTP to worker template class to avoid thread handle sharing
    [adc.cpp, barometer.cpp, hardwareConf.hpp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]
2019-11-19 add imu, not tested
2019-11-21 before debugging sdLog close on power off
2019-11-21 use reworked sdLog.c whith fixed autoflush period, works ok without dirty bit on few tries. Should be teste more thoroughly
    [adc.cpp, hardwareConf.hpp, main.cpp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]
2019-11-21 fix incorrect values of the resistors used in the power supply voltage divider
    [adc.cpp, hardwareConf.hpp]
2019-11-25 baro, adc and differential pressure emit event
2019-11-26 imu also send event, so now all sensors send events
2019-11-27 indicate that thread run only once using noreturn kw
2019-11-27 change led1 led2 by led_green led_red
    [board.cfg]
2019-11-27 use syslog instead of debug trace, write git revision and other useful info @ syslog start
2019-11-27 log all sensors data @100 hz on the sdcard
2019-11-27 fix source event : dpif instead of baro
    [sdcard.cpp]
2019-11-27 fix event was sent for each of the 3 dp sensors, but only one event is expected
    [differentialPressure.cpp]
2019-11-28 add a rough program to display sensors output
2019-11-28 red led on if anything goes wrong
    [main.cpp]
2019-11-28 clean flow control in main.cpp, simplify shell close command
2019-11-28 fix stopAllPeripherals, called in case of power supply stop. it made chibios chSysHalt, and no sdcard clean close was done
    [hardwareConf.hpp]
2019-12-03 4.4v threshold for tests before dynamic threshold
2019-12-03 dynamic shutdown threashold voltage (not tested)
2019-12-04 fix app code because of chibios fix #1060 to restore usb_storage; fix VSS initial calculation
    [adc.cpp]
2019-12-12 portage from linux to MCU fails because of embedded libc++ limitation : try to switch to etl
    [main.cpp, sdcard.cpp]
2019-12-13 initial portage completed whithout the need to switch to ETL
2019-12-14 use conf parameter for sensors initialisation parameters
2019-12-17 raise dynamic memory pool size, raise threads stack size, still memory problem with certain level of optimisation, namely -Og
    [hardwareConf.hpp, main.cpp, mcuconf.h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]
2019-12-17 remove ETL : F7 don't lack memory, and we need dynamic allocation, so we can use STL for all
2019-12-18 update todo.txt, print param alias if it exists in syslog and generated smartprobe.conf, add initial file (from crazyflies repo) for AHRS
2019-12-18 print associated alias for default value and syslog message, update todo.txt
2019-12-20 log euler angles to sdcard, with a configuration parameter to choose between raw imu and ahrs estimated euler angles
2019-12-21 calculate relative wind vector : big concern about calibration matrix orientation numpy vs eigen
2019-12-22 add parameters for SDP3X : fetch pressure and temperature, temperature getch frequency relative to pressure
2019-12-22 use ca_copy instead of copying va_list directly : more compliant, but do not resolve crashes
    [sdcard.cpp]
2019-12-23 crashes orginin is : newlib's *s*printf class of function are not reentrant (libc one are, so man say it's reentrant) : I commit a temporary fix using newlib _*s*printf_r class of function, but the r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
2019-12-23 fix potential problems : no reentrancy of newlib sprintf, protect (mutex) configuration dictionary access, preallocate std::string
    [sdcard.cpp]
2019-12-23 more precise timestamp when aquisition frequency is over >= 100hz
2019-12-24 fix va_list bug when no trace, fix no serialdatastrem when no trace
    [board.cfg]
2019-12-25 revert to STM32F777VIHx (part in board.cfg)
    [board.cfg]
2019-12-25 centralize static size of thread in file hardwareConf.hpp, fix use of parameter "ahrs.type" in sdcard.cpp
    [hardwareConf.hpp, sdcard.cpp]
2020-01-08 make all internal IMU angle be in radian, degree only used for display and ascii log. 3d wind calculus stay in degrees for now
2020-01-08 detect swdio activity, and close cleanly sdcard before entering swdio mode; put fatfs in pedantic mode : will not mount FS with dirty bit neither cluster incoherency
2020-01-22 in the streamed data (low frequency), mean attitude and air vector instead of taking one sample
2020-02-06 add capacity to send aeroprobe message to pprz via uart (not tested)
2020-02-07 add capacity to get pprz message from uart (not tested)
2020-02-07 launch uart receive thread in main.cpp when mode is PPRZ_IN_OUT
2020-02-14 add pprzlink encoder decoder files
2020-02-20 remove warning about wind velocity calculation : tested OK
2020-02-26 do no run showBB when uart is in link mode
2020-02-27 fix serial driver initialisation
2020-02-28 fix method to wait for uart initialisation
2020-03-18 create unit test for nmeaFrame modification
    [board.cfg]
2020-03-26 add configuration value : canbus id in prevision of installing many SP on a plane
2020-03-26 fix uwb swallow bug which lead to read 0 bytes on a channel (chibios trapped error)
    [SmartProbe_v003_liste_pins_labels.ods, board_v3.cfg]
2020-03-26 add schematics of V003 version of the board
    [SmartProbe_v003_liste_pins_labels.ods, board.cfg]
2020-03-30 sensorlog (TSV format) gps data if avalaible
2020-04-01 modularize TSV sensors log
2020-04-01 trace uart speed is not anymore in configuration file, add non compound statement macro since the compund one trigger a strange bug
    [main.cpp, sdcard.cpp]
2020-04-01 fix order of initialisation : get log name from configuration file
    [main.cpp, sdcard.cpp]
2020-04-02 fix chronology problem at start, move constants to hardwareConf.hpp
    [hardwareConf.hpp, main.cpp, sdcard.cpp]
2020-04-02 fix a very serious bug in dynamic memory management : operateur new and delete was not redefinded in all copilation units
    [sdcard.cpp]
2020-04-15 raise main thread stack size
2020-04-27 we do not use pwmd9
2020-06-02 fix printf format errors
    [sdcard.cpp]
2020-06-09 begin replacement of sdLog library by sdLiteLog (not finished)
    [adc.cpp, hardwareConf.hpp, sdcard.cpp]
2020-06-12 sdLiteLog finish replacement of sdLog library by sdLiteLog, tested, seems OK, need more tests
    [adc.cpp, main.cpp, sdcard.cpp]
2020-07-01 fix typo in logical test
    [imu.cpp]
2020-09-02 portage to v003 : led in the noose, voltage from battery no from 5V regulator
    [board.cfg, board_v002.cfg]
2020-09-03 v003 has two uart, one dedicated to autopilot or gps, one dedicated to debug and shell
2020-09-08 fix µsecond calculus truncated to 32 bits : was wrapping after 1 hour and 10 minutes
    [sdcard.cpp]
2020-09-08 time in binary and text log are now expressed in seconds, not milliseconds
2020-09-09 power supply is not 5V anymore, so change the label
2020-09-09 launch showBB thread only whenh TRACE is defined
2020-09-17 sample 4 adc channels
    [board.cfg]
2020-09-17 fix wrong loop bound
    [adc.cpp, mcuconf.h]
2020-09-17 do no track generated file board.h
2020-09-18 add led code for swdio mode, detect and wait
2020-09-18 periodicly check thread stack occupancy, internal voltage, core temp and log abnormal values
2020-09-22 use INT1 pin of IMU TDK20600 to trigger acquisition
    [board.cfg]
2020-09-23 remove the necessity to have STM32CubeMX by fursnishing generated board.h
2020-09-24 modify color code for nose led
2020-09-24 - smartLed is not a library component anymore - version number of syslog and sensorlog are now synchronized
2020-11-18 fix long constant (20 digits) make parser to segfault, fix no associated led error code to sdcard format not recognised
    [main.cpp]
2020-11-20 lower voltage by element threshold to avoid smartprobe unexpected shutdown during flight with nearly empty battery
    [hardwareConf.hpp, main.cpp]
2021-05-05 change internal thread parameter name to follow chibios API change
2021-05-26 °add tas parameter to the streamed pprz message °short flash the noose led after init to lower heat generation
    [sdcard.cpp, smartLed.cpp]
2021-05-26 window average static pressure and temperature to calculate rho
2021-05-26 remove debug trace
2021-09-23 add code to make led color and intensity change with relative air speed tas and alpha : does not seems to start
2021-09-24 fix led color and intensity change with relative air speed tas and alpha
    [main.cpp, smartLed.cpp]
2024-11-29 update README.md
    fix typos in README.md
    more typos fix in README.md
    [SmartProbe_v003_liste_pins_labels.ods]
2024-12-03 add hardware description directory
    [SmartProbe_v004.kicad_pcb, SmartProbe_v004.kicad_sch, SmartProbe_v004_cap.STL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]

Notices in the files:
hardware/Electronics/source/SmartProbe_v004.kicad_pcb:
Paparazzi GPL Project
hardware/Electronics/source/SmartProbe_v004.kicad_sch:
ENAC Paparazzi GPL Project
